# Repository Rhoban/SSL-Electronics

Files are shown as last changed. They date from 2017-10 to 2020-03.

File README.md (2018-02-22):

# SSL Boards

## Compiling firmware

Be sure you follow the README.md from https://github.com/Rhoban/Maple/ to have the prerequisite.

You can clone the `Maple` repository, for instance in your home:

    git clone git@github.com:Rhoban/Maple.git

Then, go in the firmware directory (for instance in brushless or in mainboard) and make a symlink to it:

    ln -s $HOME/Maple Maple

You can then compile and install:

    make
    make install

-------------------------------------------------

## Components

You can find most of the component source in the `FARNELL` attribute of each component.

### Main board

### Connectors

* JST-ZH 2 pin connector + cables
* JST-XH 7 pins connector for kicker board
* XT-60 connector (same as wire connector)

#### Maple mini

Board containing micro-controller (mainboard controller)

#### GY-85

9DOF IMU

#### nRF24L01 modules

2.4Ghz communication modules with short antenna (Farnell: 2143316)

### Screws

* M3 holes are on the board, on a 126x82mm rectangle.
* M3x10 spacers can be used to hold the drivers on the board

-------------------------------------------------

## Brushless driver

### Connectors

* JST-ZH 5 pin connector (for hall sensor)
* JST-ZH 6 pin connector (for encoder)
* JST-XH 3 pin connector (for motor phases)

-------------------------------------------------

## Kicker board

### Power capacitor

Power capacitors, current target is 2200uF / 200V (2102441)

### Connectors

* JST-XH 7 pins connector

#### Voltage booster

Can be easily found with keywords "390V booster"

### Screws

M3 spacers to fix the board

-------------------------------------------------

## Misc

#### Fuses

F447 fuses on the wire are used to protect

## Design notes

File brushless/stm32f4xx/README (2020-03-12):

> Copyright (C) 2019  Adrien Boussicault <adrien.boussicault@labri.fr>
>
> This program is free software: you can redistribute it and/or
> modify it under the terms of the GNU Lesser General Public
> License as published by the Free Software Foundation, either
> version 3 of the License, or (at your option) any later version.
>
> This program is distributed in the hope that it will be useful,
> but WITHOUT ANY WARRANTY; without even the implied warranty of
> MERCHANTABILITY or FITNESS FOR A PARTICULAR PURPOSE.  See the GNU
> Lesser General Public License for more details.
>
> You should have received a copy of the GNU Lesser General Public
> License along with this program.  If not, see
> <http://www.gnu.org/licenses/>.

This documentation explains how to compile the firmware of the brushless 
board, and how to flash the brushless board, by using a Linux Operating System.

##################
# Installation : #
##################

Installation commands are for Debian or Ubuntu.

Install the following package :
-------------------------------

sudo apt-get install dfu-util cu build-essential python-serial r-base

Install R libraries : 
---------------------

./tools/logs/install.r

Uninstall the modemmanager : 
----------------------------

sudo apt-get remove modemmanager

( The modemManger will grab the serial line of the USB : /dev/ttyACM0;
if you are using this service, you should prefer do desactivate them with the
following command : systemctl stop ModemManager.service )

Add Udev permition to have an access to /dev/ttyACMO
----------------------------------------------------

sudo adduser USER plugdev
sudo adduser USER dialout

Add/edit the file /etc/udev/rules.d/42-cycloide.rules and add the following 
lines :

ATTRS{idProduct}=="4567", ATTRS{idVendor}=="f123", MODE="664", GROUP="plugdev" SYMLINK+="brushless"
ATTRS{idProduct}=="5740", ATTRS{idVendor}=="0483", MODE="664", GROUP="plugdev" SYMLINK+="stm32"

The first line is dedicated to comunicate with the brushless when the firmware
is yet loaded in the board. The second one is used to flash the firmware.

Restart the udev service :
 
sudo /etc/init.d/udev restart

Normally, all should works but if you enconter some problem in the next sections, restart your computer.

Download ans install the last ARM compiler :
--------------------------------------------------

We use the gcc-arm-none-eabi compiler. You can download it at :

https://developer.arm.com/tools-and-software/open-source-software/developer-tools/gnu-toolchain/gnu-rm/downloads

Install the compiler in the root directory of the project.

You can install the compiler in another directory. In this case, 
we will explain you, in all the next sections, how to adapt the commands.

Normally, the project should looks like :
<root_directory>
├── Core
├── gcc-arm-none-eabi-XXXXXXXXX
│   ├── bin
│   ...
├── Makefile
...

Download the CMSIS source code :
--------------------------------

Install the CMSIS library in the root directory by typing :

git clone https://github.com/ARM-software/CMSIS_5.git CMSIS_5

You can install the compiler in another directory. In this case, 
we will explain you, in all the next sections, how to adapt the commands.

Normally, the project should looks like :
<root_directory>
├── Core
├── CMSIS_5
│   ├── CMSIS
│   ...
├── Makefile
...

OPTIONAL INSTALLATION (to use JTAG):
-------------------------------------

You can install JLink tools in order to use JTAG to flash or print.
Go to the website :  

https://www.segger.com/downloads/jlink/

And install the J-Link Software and Documentation Pack :
    - download the debian package (file finishing with .deb)
    - install it : sudo dpkg --install XXX.deb
      where XXX.deb is the name downloaded file.

OPTIONAL INSTALLAION OF CUBEMX (to update the source code autgenerated by cubeMX ):
-----------------------------------------------------------------------------------

If you want to change the configuration generated by CUBEMX, you have to install
CubeMX for the following website :

https://www.st.com/en/development-tools/stm32cubemx.html

#########################################
# Compile the application               #
#########################################

Just type

make

If you have installed GCC and CMSIS in an unusual place, then you have to type :

make GCC_PATH=<ARM_DIRECTORY>/bin CMSIS_PATH=<CMSIS_5_PATH>/CMSIS

otherwise, you just have to add two symbolic links in your root directory :

cd <root directory>
ln -s ARM_DIRECTIRY gcc-arm-none-eabi
ln -s CMSIS_5_DIRECTIRY CMSIS_5

###################
# Flash the board #
###################

Three solutions are possible depending of the situation.
IF THE BOARD HAVE NOT YET BEEN FLASHED, YOU SHOULD USE (as you want) SOLUTION 
1) OR 2).
Solution 3) is the most simple one and it is used to update the firmware (we 
need the board to be yet flashed).

Short description of the 3 solutions : 
 1) FLASH BY USB USING THE RESET AND BOOT0 BUTTONS
   This solution doesn't need the board to be yet flashed.
   This solution need USB wire and and an access to the BOOT0 and RESET buttons
   of the board.
 2) FLASH BY JTAG USING THE JLink SOFWTARE
   This solution doesn't need the board to be yet flashed.
   This solution need an USB wire (for the power) and a JTAG for the connection.
   This solution Use JLink software (see Optional installation)
   The JLink software downloads just the part of the memory that have changed.
   So the flash operation are fast and the life of the flash memory is 
   increased.
 3) FLASH BY USB WITHOUT USING THE RESET BUTTONS
   This solution need the board to be yet flashed
   ( by using 1) or 2) for example ).
   This solution just need a USB wire ! :)
   This solution DO NOT require an acess to the BOOT0 and RESET button ! :)

1) FLASH BY USB USING THE RESET AND BOOT0 BUTTONS

 Connect the USB wire.

 Press and hold the BOOT0 button, then press and realease de RESET button,
 and finally release the BOOT0 button.

 Type the command :
 ./first_flash_with_usb_and_reset_button.sh

2) FLASH BY JTAG USING THE JLink SOFWTARE

 ./jtag_flash.sh

3) FLASH BY USB WITHOUT THE RESET BUTTONS

 ./usb_flash.sh

########################
# Connect to the board #
########################

First Connect the USB wire.

To know on which device the board is connected (usualy it is /dev/ttyACM0),
you have to execute the following command :

dmesg

The output should looks like : 

   [112520.828609] usb 1-5: new full-speed USB device number 59 using xhci_hcd
   [112520.979771] usb 1-5: New USB device found, idVendor=f123, idProduct=4567, bcdDevice= 2.00
   [112520.979777] usb 1-5: New USB device strings: Mfr=1, Product=2, SerialNumber=3
   [112520.979780] usb 1-5: Product: Brushless Driver
   [112520.979783] usb 1-5: Manufacturer: OpenHandicap
   [112520.979785] usb 1-5: SerialNumber: 346F398B3038
   [112520.981964] cdc_acm 1-5:1.0: ttyACM0: USB ACM device

and the serial port is ttyACM0, so the device is connected on (/def/ttyACM0).

Open a command line into the board by typing:

cu -l /dev/ttyACM0

Your are connected to the boare. Enjoy :) 
(In the command line, help is the first helpfull command to know)
(type 'led' to turn on/off the led of the board) 

OPTIONAL :
----------
Some informations are sent using the jtag link. (just some small messages 
to prevent warnings and errors). Those messages appear in the terminal too.

If you want to read the jtag output, you need to install JLink (see the
optional section on JTag), and then, you just have to type : 

./print_jtag

Jtag is usefull for developpers.

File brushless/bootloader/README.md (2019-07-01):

# Maple Bootloader for Robotis boards

This is an adaptation of the maple bootloader in order to make it work with the
Robotis CM900 and OpenCM9.04 boards:

* [Robotis CM900](http://support.robotis.com/en/product/auxdevice/controller/cm-900_manual.htm)
* [Robotis OpenCM9.04](http://support.robotis.com/en/product/auxdevice/controller/opencm9.04.htm)

## How to install it?

### The easy way

#### OpenCM9.04

The easy way is to use a simple sketch with the robotis OpenCM Framework to do it. Simply run
OpenCM IDE and open the `opencm904_maple_loader` sketch that is in the `sketch/` directory of
this repository.

**If you load that sketch, it will rewrite your bootloader to the OpenCM9.04 bootloader;
OpenCM IDE won't work anymore!**

Wait until your board led blinks, and your bootloader should be changed. You can press the reset
button and you should see the "bootloader blink".

### The standard way

#### Step 1. Build or get the right bootloader

You can either build it or get it (from the `snapshot` directory). See below.

#### Step 2. Wire a serial line to your board

This step may require some soldering or electronic hacking, you'll have to wire up a serial 3.3V 
adapter. You can for instance use a [3.3V FTDI cable](http://www.ftdichip.com/Products/Cables/USBTTLSerial.htm)
or a [3.3V FTDI Breakout](https://www.sparkfun.com/products/retired/8772). 5V logic should also
work with this.

Then, wire your serial adapter to the Serial1 (TX1 and RX1) pins of your board.

#### Step 3. Put your board in hardware bootloader mode

Press the RESET button of your board, and then put the BOOT0 signal to 3.3V (this can be done
with an extra wire), release the RESET button, and release the BOOT0.

#### Step 4. Flash the bootloader!

You can now flash the bootloader:

```
# You may have to adapt the serial port, this is an example:
python stm32loader.py -p /dev/ttyUSB -evw bootloader.bin
```

Tada! It should then be OK.

### What's next?

Next, you can program your board using `dfu-util`. This is done by default in the libmaple
Makefile.

You can now use `cm900` and `opencm904` variants in the LibMaple, or use the RobotsWar 
framework
https://github.com/RobotsWar/RobotsWar

## Boards

### CM900

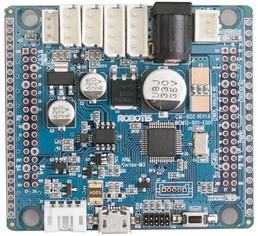
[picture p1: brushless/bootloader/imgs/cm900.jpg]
CM900


The `master` branch of this repository is supporting CM900 board, you can find a
snapshot of the bootloader in `snapshot/maple-boot-cm900.bin`.

### OpenCM9.04

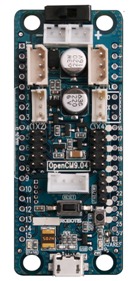
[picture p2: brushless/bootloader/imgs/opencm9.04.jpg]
OpenCM9.04


Ths `opencm904` branch of this repository is supporting the OpenCM9.04 board. You can
find a snapshot of this bootloader in `snapshot/maple-boot-opencm904.bin`.

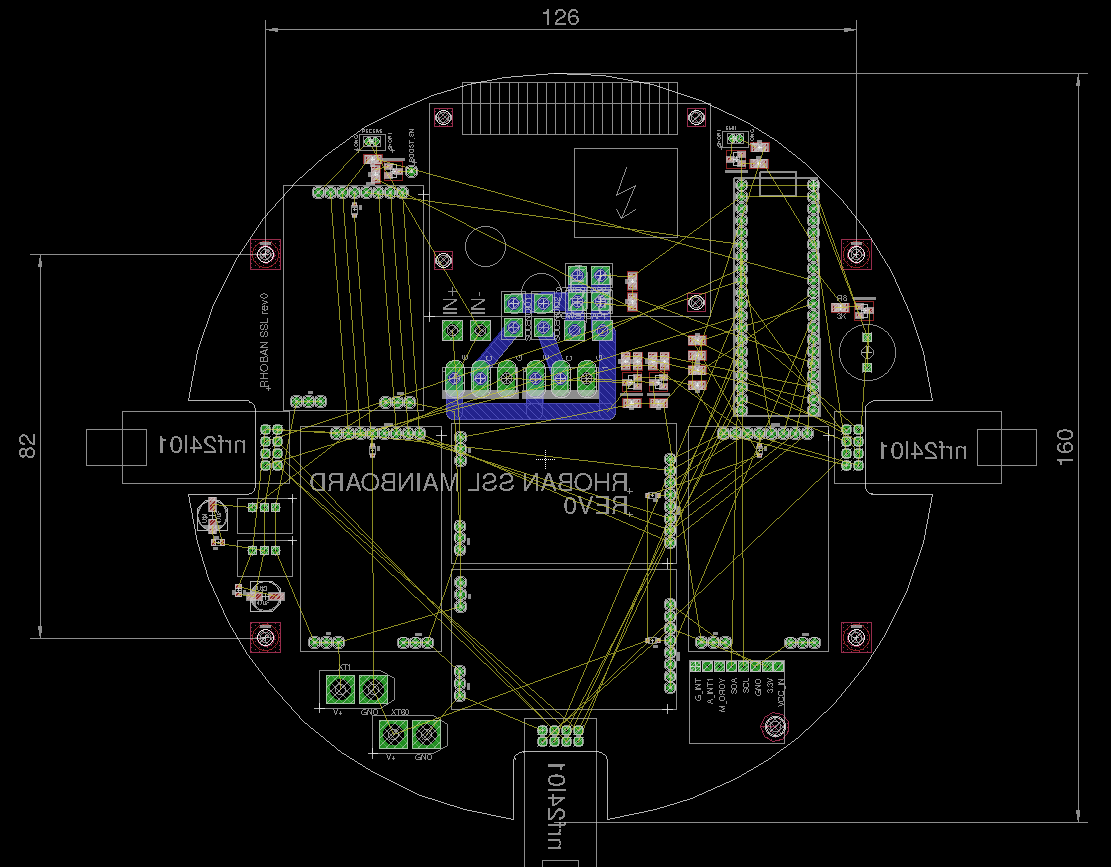
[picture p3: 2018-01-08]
mainboard/dimensions.png

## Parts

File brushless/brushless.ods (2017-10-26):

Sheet: brushless
Farnell | Name | Value | Device | Package
1437637 | BUT | KMR211GLFS | BUTTON-KMR241GLFS | PUSHBUTTON-KMR241GLFS
2528772 | C1 | 10µF | 0.33UF/330NF-0805-50V-10% | 805
2528772 | C2 | 10µF | 0.33UF/330NF-0805-50V-10% | 805
2528772 | C3 | 10µF | 0.33UF/330NF-0805-50V-10% | 805
2496935 | C4 | 1000pF | CAP0805 | 0805@1
2496946 | C7 | 1uF | CAP0805 | 0805@1
1144713 | C10 | 100uF | CPOL_EU_3.5-8 | E3,5-8
2496946 | C12 | 1uF | CAP0805 | 0805@1
721980 | C17 | 15pF | C_EU_22PF | C0603
721980 | C18 | 15pF | C_EU_22PF | C0603
1414620 | C20 | 18pF | CAP0805 | 0805@1
1414620 | C21 | 18pF | CAP0805 | 0805@1
2317446 | D1 |  | ZETEX_VAR2SOT23 | ZETEX_SOT-23
2317446 | D2 |  | ZETEX_VAR2SOT23 | ZETEX_SOT-23
2317446 | D3 |  | ZETEX_VAR2SOT23 | ZETEX_SOT-23
1581233 | D4 | Blue | LED1206 | LED-1206
8737843RL | D5 |  | DIODESOD | SOD-323
2296000 | DRV1 | OPEN-BLDC_IR2101 | OPEN-BLDC_IR2101 | OPEN-BLDC_SO-8
2296000 | DRV2 | OPEN-BLDC_IR2101 | OPEN-BLDC_IR2101 | OPEN-BLDC_SO-8
2296000 | DRV3 | OPEN-BLDC_IR2101 | OPEN-BLDC_IR2101 | OPEN-BLDC_SO-8
- | ENC1 | LS7366RSO14 | LS7366RSO14 | SO14
1022248 | GND | CONNEC_1X03 | CONNEC_1X03 | CONNEC_1X03
- | JP1 | JUMPER-SMT_2_NO_NO-SILK_ROUND | JUMPER-SMT_2_NO_NO-SILK_ROUND | SMT-JUMPER_2_NO_NO-SILK_ROUND
- | JP2 | JUMPER-SMT_2_NO_NO-SILK_ROUND | JUMPER-SMT_2_NO_NO-SILK_ROUND | SMT-JUMPER_2_NO_NO-SILK_ROUND
2470830 | K1 |  | 614105150721 | 614105150721
1022256 | LOGIC | CONNEC_1X08 | CONNEC_1X08 | CONNEC_1X08
2467818 | OSC | 8MHz | CRYSTAL5X3 | CRYSTAL-SMD-5X3
1842013 | OSC1 | 40Mhz | CRYSTAL5X3 | CRYSTAL-SMD-5X3
2319916 | Q1 | BUK7Y12-40E | BUK7Y12-40E | SOT669
2319916 | Q2 | BUK7Y12-40E | BUK7Y12-40E | SOT669
2319916 | Q3 | BUK7Y12-40E | BUK7Y12-40E | SOT669
2319916 | Q4 | BUK7Y12-40E | BUK7Y12-40E | SOT669
2319916 | Q5 | BUK7Y12-40E | BUK7Y12-40E | SOT669
2319916 | Q6 | BUK7Y12-40E | BUK7Y12-40E | SOT669
2446904 | R1 | 1K | RESISTOR0805 | 805
2446904 | R2 | 1K | RESISTOR0805 | 805
2446904 | R3 | 1K | RESISTOR0805 | 805
2446904 | R4 | 1K | RESISTOR0805 | 805
2446904 | R5 | 1K | RESISTOR0805 | 805
2446904 | R6 | 1K | RESISTOR0805 | 805
2447553 | R7 | 10K | RESISTOR0805 | 805
2447553 | R8 | 10K | RESISTOR0805 | 805
2447553 | R9 | 10K | RESISTOR0805 | 805
2447553 | R10 | 10K | RESISTOR0805 | 805
2447553 | R11 | 10K | RESISTOR0805 | 805
2447553 | R12 | 10K | RESISTOR0805 | 805
2447553 | R14 | 10K | RESISTOR0805 | 805
2447553 | R15 | 10K | RESISTOR0805 | 805
2447553 | R16 | 10K | RESISTOR0805 | 805
2447553 | R17 | 10K | RESISTOR0805 | 805
2447553 | R18 | 10K | RESISTOR0805 | 805
2447553 | R19 | 10K | RESISTOR0805 | 805
2446939 | R20 | 2K | RESISTOR0805 | 805
2446965 | R21 | 3K | RESISTOR0805 | 805
2447553 | R23 | 10K | RESISTOR0805 | 805
2447553 | R24 | 10K | RESISTOR0805 | 805
2447553 | R25 | 10K | RESISTOR0805 | 805
2446909 | R28 | 1.5K | RESISTOR0805 | 805
2446926 | R29 | 22 | RESISTOR0805 | 805
2446926 | R35 | 22 | RESISTOR0805 | 805
2446904 | R36 | 1K | RESISTOR0805 | 805
2446904 | R39 | 1K | RESISTOR0805 | 805
2447553 | R40 | 10K | RESISTOR0805 | 805
2447553 | R48 | 10K | RESISTOR0805 | 805
2446904 | R49 | 1K | RESISTOR0805 | 805
2447553 | R50 | 10K | RESISTOR0805 | 805
7261403 | REG1 | TS2940CW-3.3RP | TS2940CW-3.3RP | SOT223
1437637 | RESET | KMR211GLFS | BUTTON-KMR241GLFS | PUSHBUTTON-KMR241GLFS
1329624 | SENSE | ACS712 | ACS712 | SO8
1606327 | UC1 | STM32F103CBT6 | STM32F103CB | LQFP48
1022248 | V+ | CONNEC_1X03 | CONNEC_1X03 | CONNEC_1X03
- | X1 | JST-XH-10-PIN-LONG-PAD | JST-XH-10-PIN-LONG-PAD | JST-XH-10-PACKAGE-LONG-PAD

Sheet: Pivot Table_brushless_1
Farnell | Name | Value | Device | Package | (empty)
721980 | C17 | 15pF | C_EU_22PF | C0603
 | C18 | 15pF | C_EU_22PF | C0603
1022248 | GND | CONNEC_1X03 | CONNEC_1X03 | CONNEC_1X03
 | V+ | CONNEC_1X03 | CONNEC_1X03 | CONNEC_1X03
1022256 | LOGIC | CONNEC_1X08 | CONNEC_1X08 | CONNEC_1X08
1144713 | C10 | 100uF | CPOL_EU_3.5-8 | E3,5-8
1329624 | SENSE | ACS712 | ACS712 | SO8
1414620 | C20 | 18pF | CAP0805 | 0805@1
 | C21 | 18pF | CAP0805 | 0805@1
1437637 | BUT | KMR211GLFS | BUTTON-KMR241GLFS | PUSHBUTTON-KMR241GLFS
 | RESET | KMR211GLFS | BUTTON-KMR241GLFS | PUSHBUTTON-KMR241GLFS
1581233 | D4 | Blue | LED1206 | LED-1206
1606327 | UC1 | STM32F103CBT6 | STM32F103CB | LQFP48
1842013 | OSC1 | 40Mhz | CRYSTAL5X3 | CRYSTAL-SMD-5X3
2296000 | DRV1 | OPEN-BLDC_IR2101 | OPEN-BLDC_IR2101 | OPEN-BLDC_SO-8
 | DRV2 | OPEN-BLDC_IR2101 | OPEN-BLDC_IR2101 | OPEN-BLDC_SO-8
 | DRV3 | OPEN-BLDC_IR2101 | OPEN-BLDC_IR2101 | OPEN-BLDC_SO-8
2317446 | D1 | (empty) | ZETEX_VAR2SOT23 | ZETEX_SOT-23
 | D2 | (empty) | ZETEX_VAR2SOT23 | ZETEX_SOT-23
 | D3 | (empty) | ZETEX_VAR2SOT23 | ZETEX_SOT-23
2319916 | Q1 | BUK7Y12-40E | BUK7Y12-40E | SOT669
 | Q2 | BUK7Y12-40E | BUK7Y12-40E | SOT669
 | Q3 | BUK7Y12-40E | BUK7Y12-40E | SOT669
 | Q4 | BUK7Y12-40E | BUK7Y12-40E | SOT669
 | Q5 | BUK7Y12-40E | BUK7Y12-40E | SOT669
 | Q6 | BUK7Y12-40E | BUK7Y12-40E | SOT669
2446904 | R1 | 1K | RESISTOR0805 | 805
 | R2 | 1K | RESISTOR0805 | 805
 | R3 | 1K | RESISTOR0805 | 805
 | R36 | 1K | RESISTOR0805 | 805
 | R39 | 1K | RESISTOR0805 | 805
 | R4 | 1K | RESISTOR0805 | 805
 | R49 | 1K | RESISTOR0805 | 805
 | R5 | 1K | RESISTOR0805 | 805
 | R6 | 1K | RESISTOR0805 | 805
2446909 | R28 | 1.5K | RESISTOR0805 | 805
2446926 | R29 | 22 | RESISTOR0805 | 805
 | R35 | 22 | RESISTOR0805 | 805
2446939 | R20 | 2K | RESISTOR0805 | 805
2446965 | R21 | 3K | RESISTOR0805 | 805
2447553 | R10 | 10K | RESISTOR0805 | 805
 | R11 | 10K | RESISTOR0805 | 805
 | R12 | 10K | RESISTOR0805 | 805
 | R14 | 10K | RESISTOR0805 | 805
 | R15 | 10K | RESISTOR0805 | 805
 | R16 | 10K | RESISTOR0805 | 805
 | R17 | 10K | RESISTOR0805 | 805
 | R18 | 10K | RESISTOR0805 | 805
 | R19 | 10K | RESISTOR0805 | 805
 | R23 | 10K | RESISTOR0805 | 805
 | R24 | 10K | RESISTOR0805 | 805
 | R25 | 10K | RESISTOR0805 | 805
 | R40 | 10K | RESISTOR0805 | 805
 | R48 | 10K | RESISTOR0805 | 805
 | R50 | 10K | RESISTOR0805 | 805
 | R7 | 10K | RESISTOR0805 | 805
 | R8 | 10K | RESISTOR0805 | 805
 | R9 | 10K | RESISTOR0805 | 805
2467818 | OSC | 8MHz | CRYSTAL5X3 | CRYSTAL-SMD-5X3
2470830 | K1 | (empty) | 614105150721 | 614105150721
2496935 | C4 | 1000pF | CAP0805 | 0805@1
2496946 | C12 | 1uF | CAP0805 | 0805@1
 | C7 | 1uF | CAP0805 | 0805@1
2528772 | C1 | 10µF | 0.33UF/330NF-0805-50V-10% | 805
 | C2 | 10µF | 0.33UF/330NF-0805-50V-10% | 805
 | C3 | 10µF | 0.33UF/330NF-0805-50V-10% | 805
7261403 | REG1 | TS2940CW-3.3RP | TS2940CW-3.3RP | SOT223
- | ENC1 | LS7366RSO14 | LS7366RSO14 | SO14
 | JP1 | JUMPER-SMT_2_NO_NO-SILK_ROUND | JUMPER-SMT_2_NO_NO-SILK_ROUND | SMT-JUMPER_2_NO_NO-SILK_ROUND
 | JP2 | JUMPER-SMT_2_NO_NO-SILK_ROUND | JUMPER-SMT_2_NO_NO-SILK_ROUND | SMT-JUMPER_2_NO_NO-SILK_ROUND
 | X1 | JST-XH-10-PIN-LONG-PAD | JST-XH-10-PIN-LONG-PAD | JST-XH-10-PACKAGE-LONG-PAD
8737843RL | D5 | (empty) | DIODESOD | SOD-323
Total Result

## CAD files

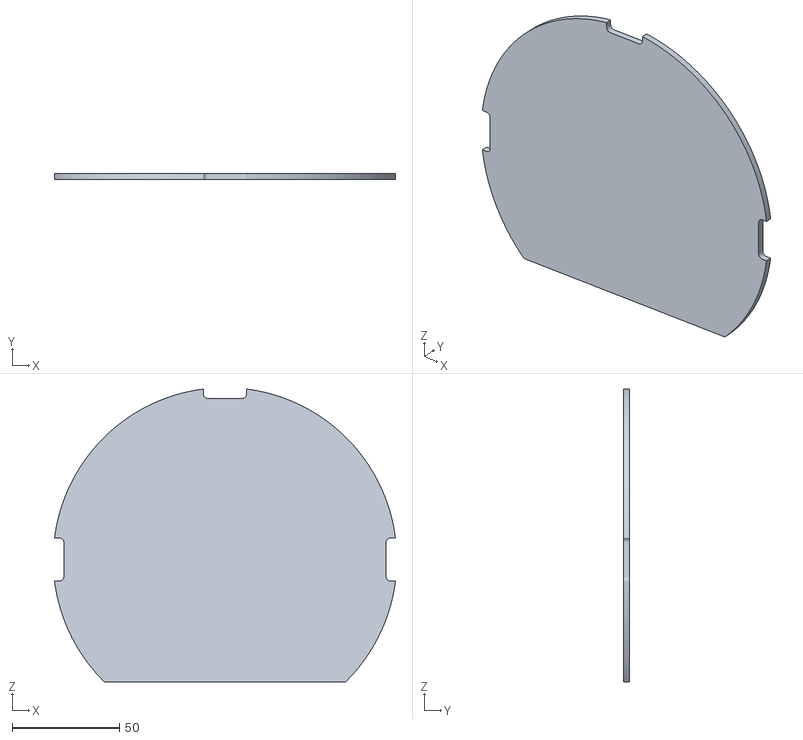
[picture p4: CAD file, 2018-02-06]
mainboard/shape/board.stl
158.7 x 3.00 x 136.4

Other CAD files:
mainboard/shape/board.dxf
mainboard/shape/board.ipt

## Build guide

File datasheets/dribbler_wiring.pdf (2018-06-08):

# Dribbler wiring

## Dribbler Connection

Brown
Red
Orange

Yellow
Green
Blue
Violet
Grey

JST-XH black (ext)
JST-XH black (mid.)
JST-XH red

Hall black
Hall red
Hall yellow
Hall green
Hall blue

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
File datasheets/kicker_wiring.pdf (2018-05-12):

Kicker board
connector view

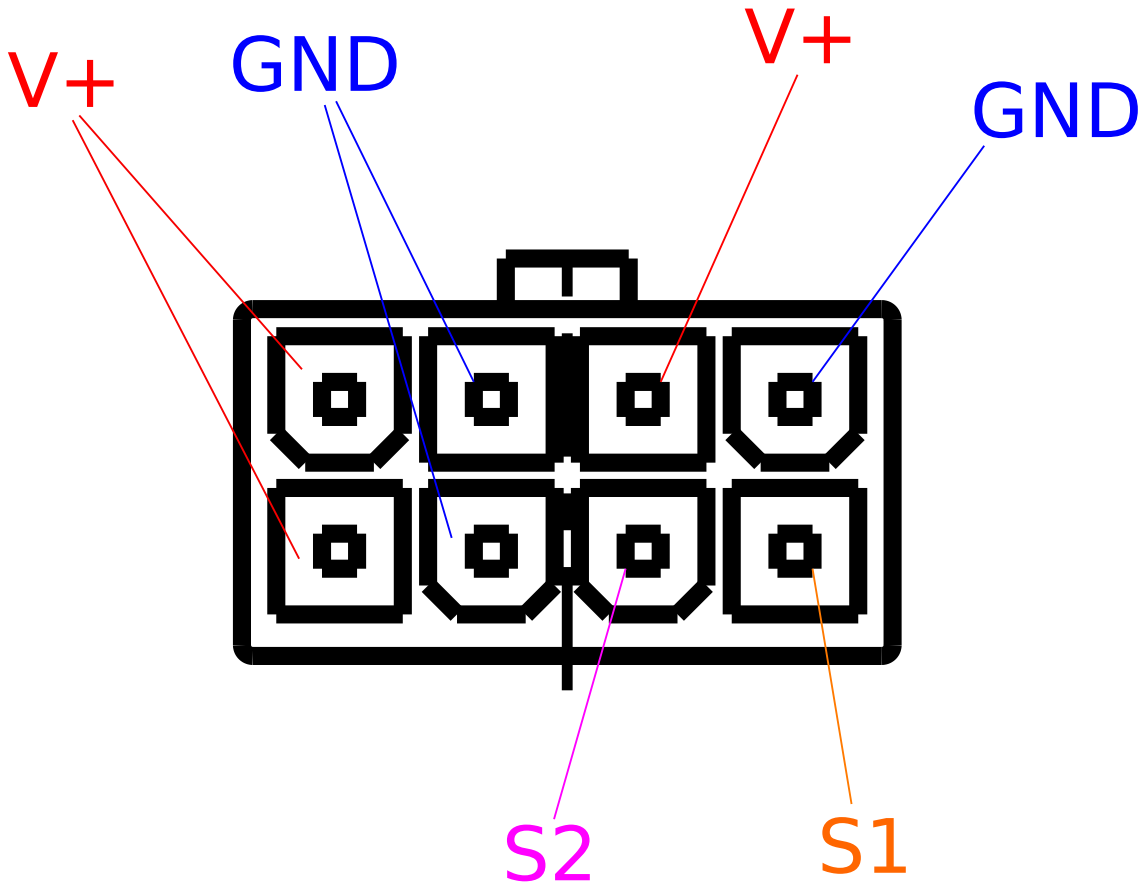
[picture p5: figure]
GND

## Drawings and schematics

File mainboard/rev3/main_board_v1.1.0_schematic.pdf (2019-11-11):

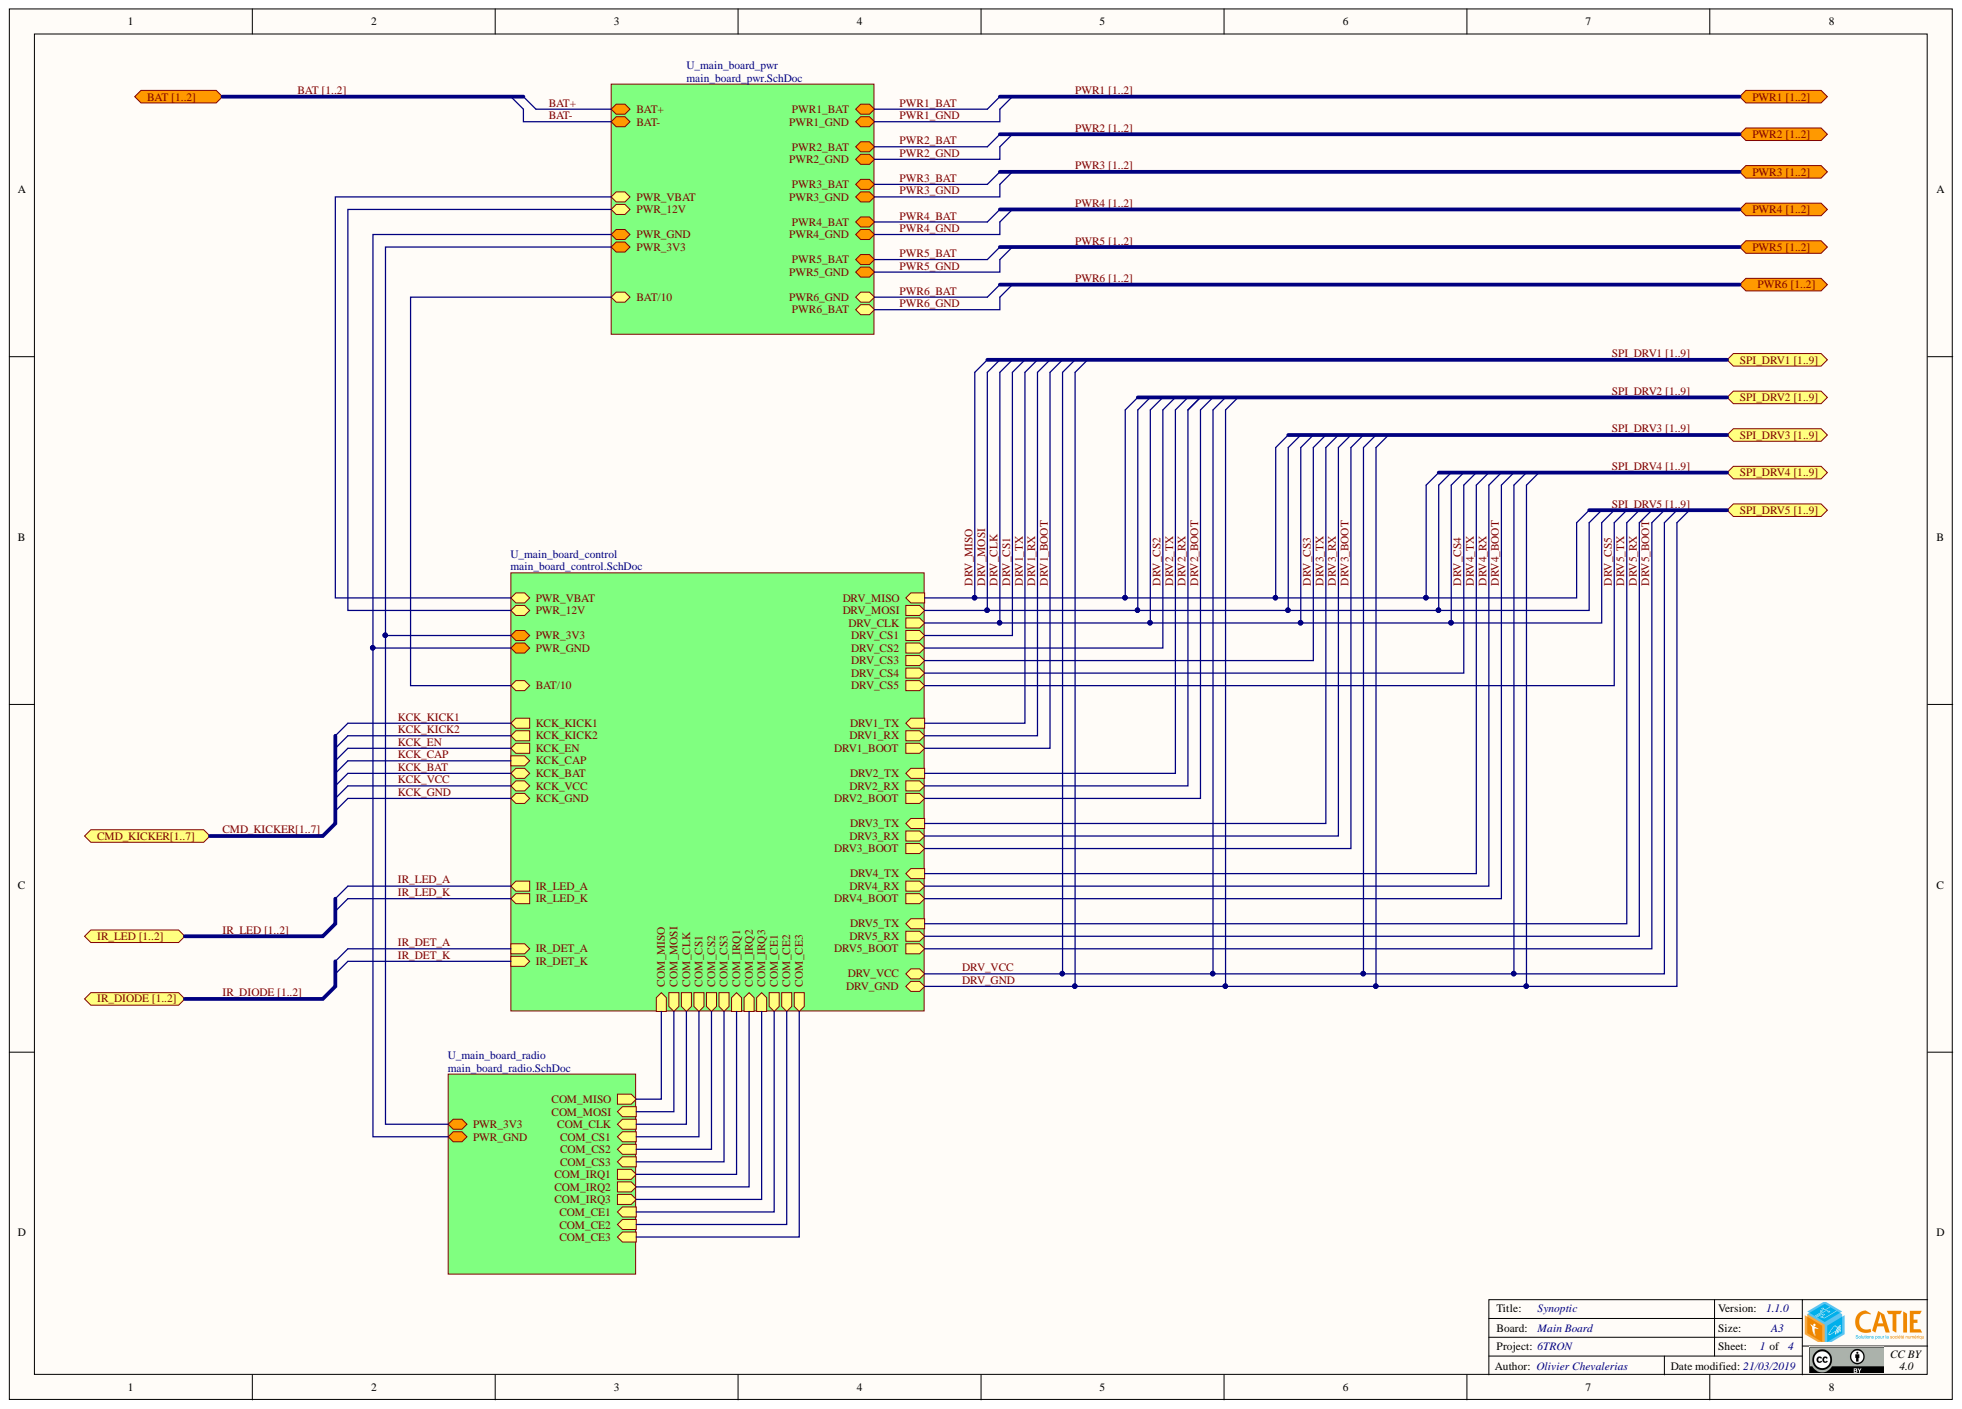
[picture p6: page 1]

PWR_VBAT PWR_12V

PWR_3V3

KCK_KICK2
KCK_EN
KCK_CAP
KCK_BAT
KCK_VCC
KCK_GND

IR_LED_A
IR_LED_K

IR_DET_A
IR_DET_K | DRV_VCC

Title: Synoptic | Version: 1.1.0
Board: Main Board | Size: A3
Project: 6TRON | Sheet: 1 of 4
Author: Olivier Chevalerias | Date modified: 21/03/2019

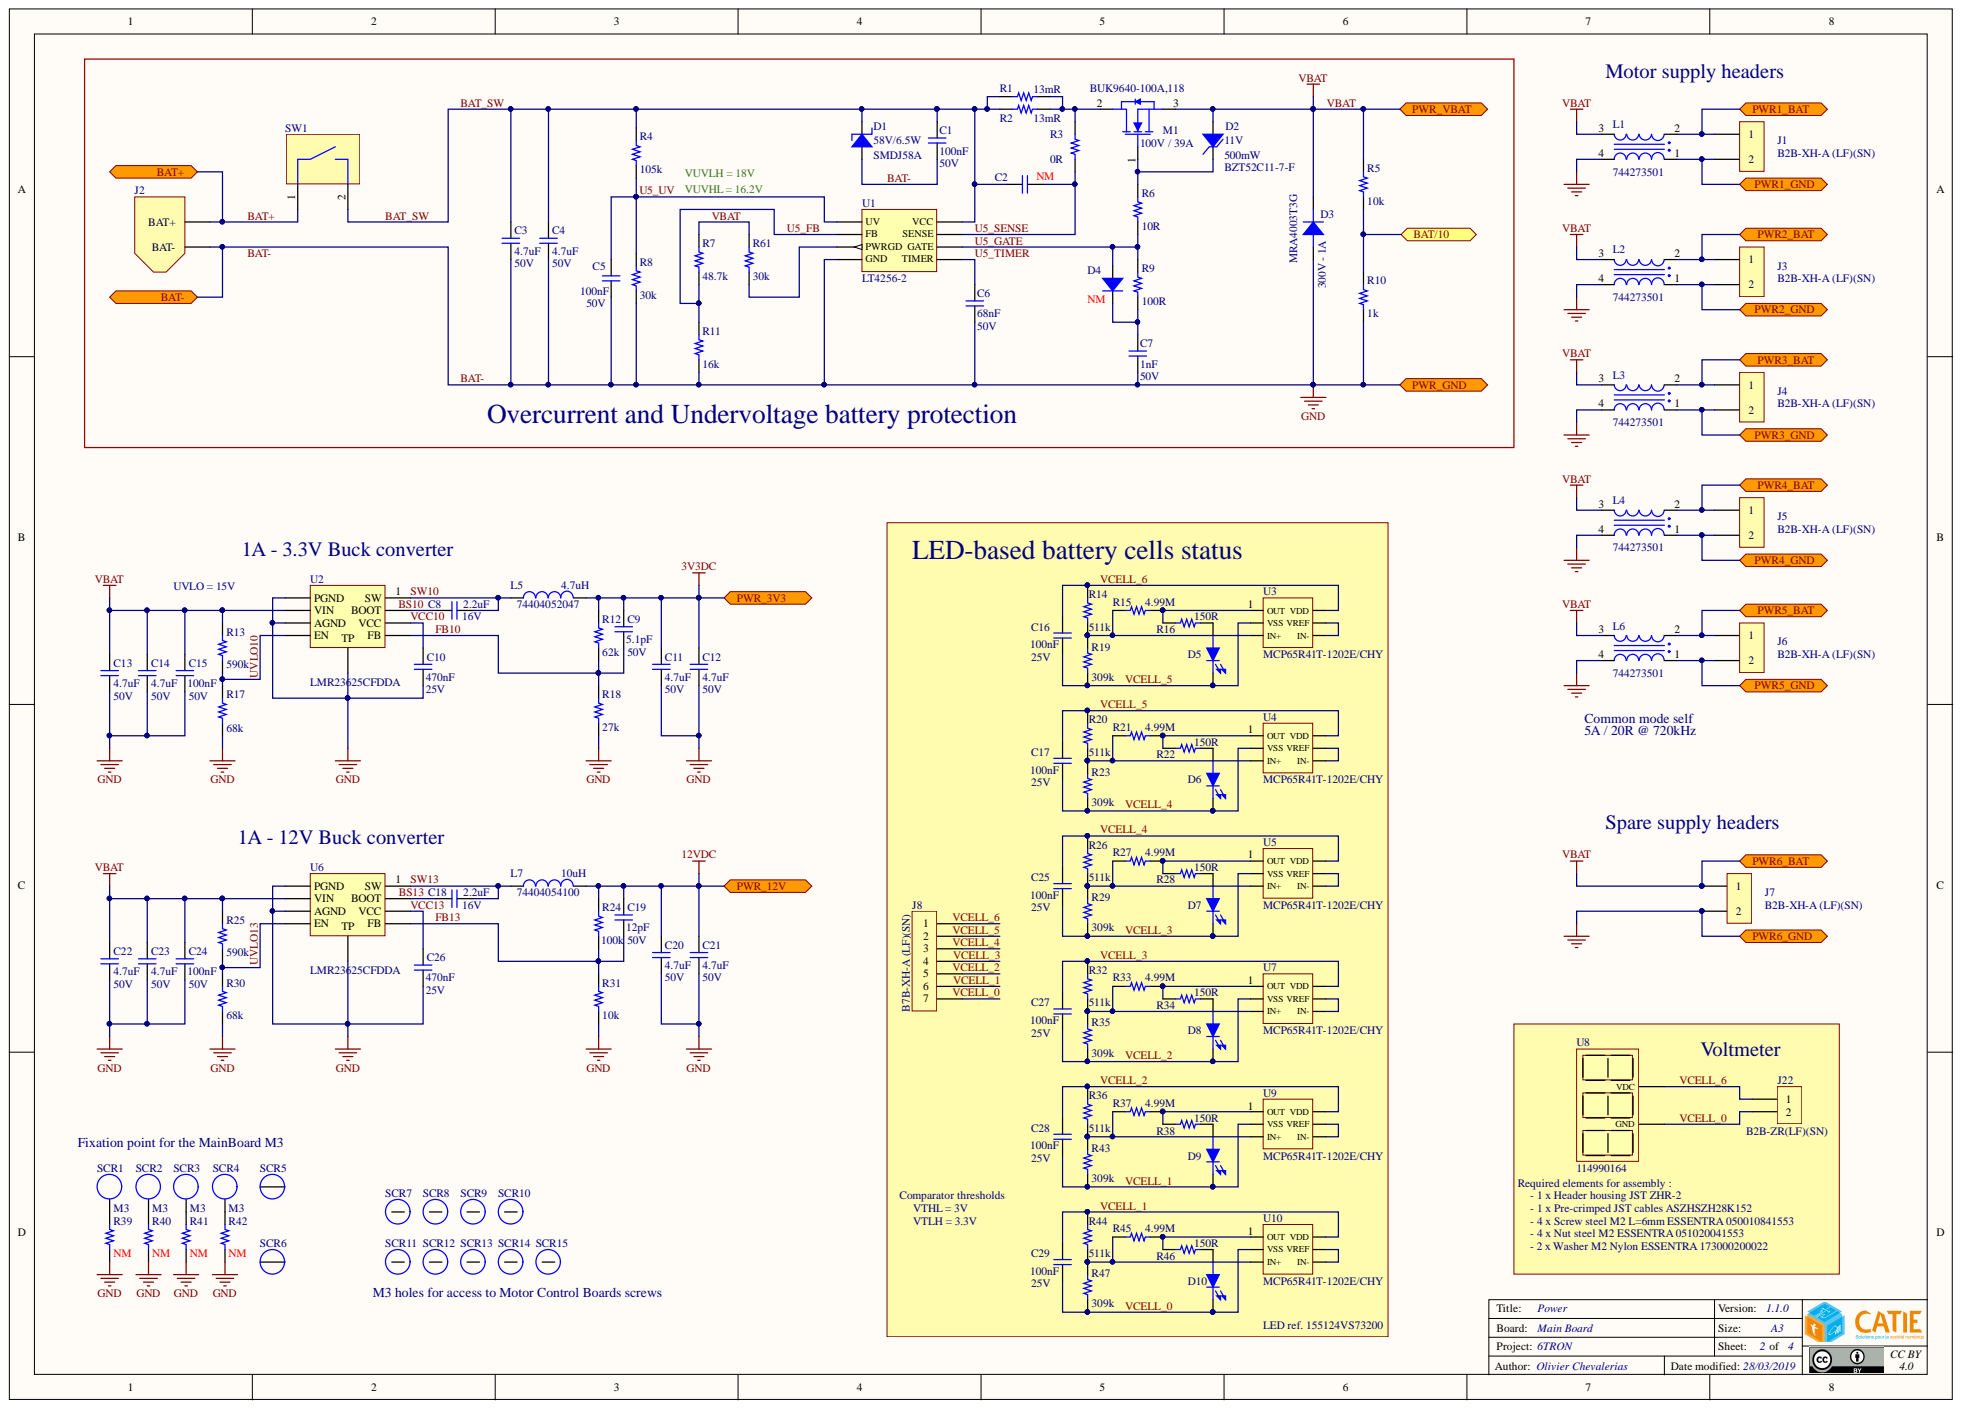
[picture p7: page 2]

BAT-
Overcurrent and Undervoltage battery protection

LED-based battery cells status

Fixation point for the MainBoard M3

Required elements for assembly :
- 1 x Header housing JST ZHR-2
- 1 x Pre-crimped JST cables ASZHSZH28K152

M3 holes for access to Motor Control Boards screws

Project: 6TRON | 2 4

Olivier Chevalerias | 28/03/2019

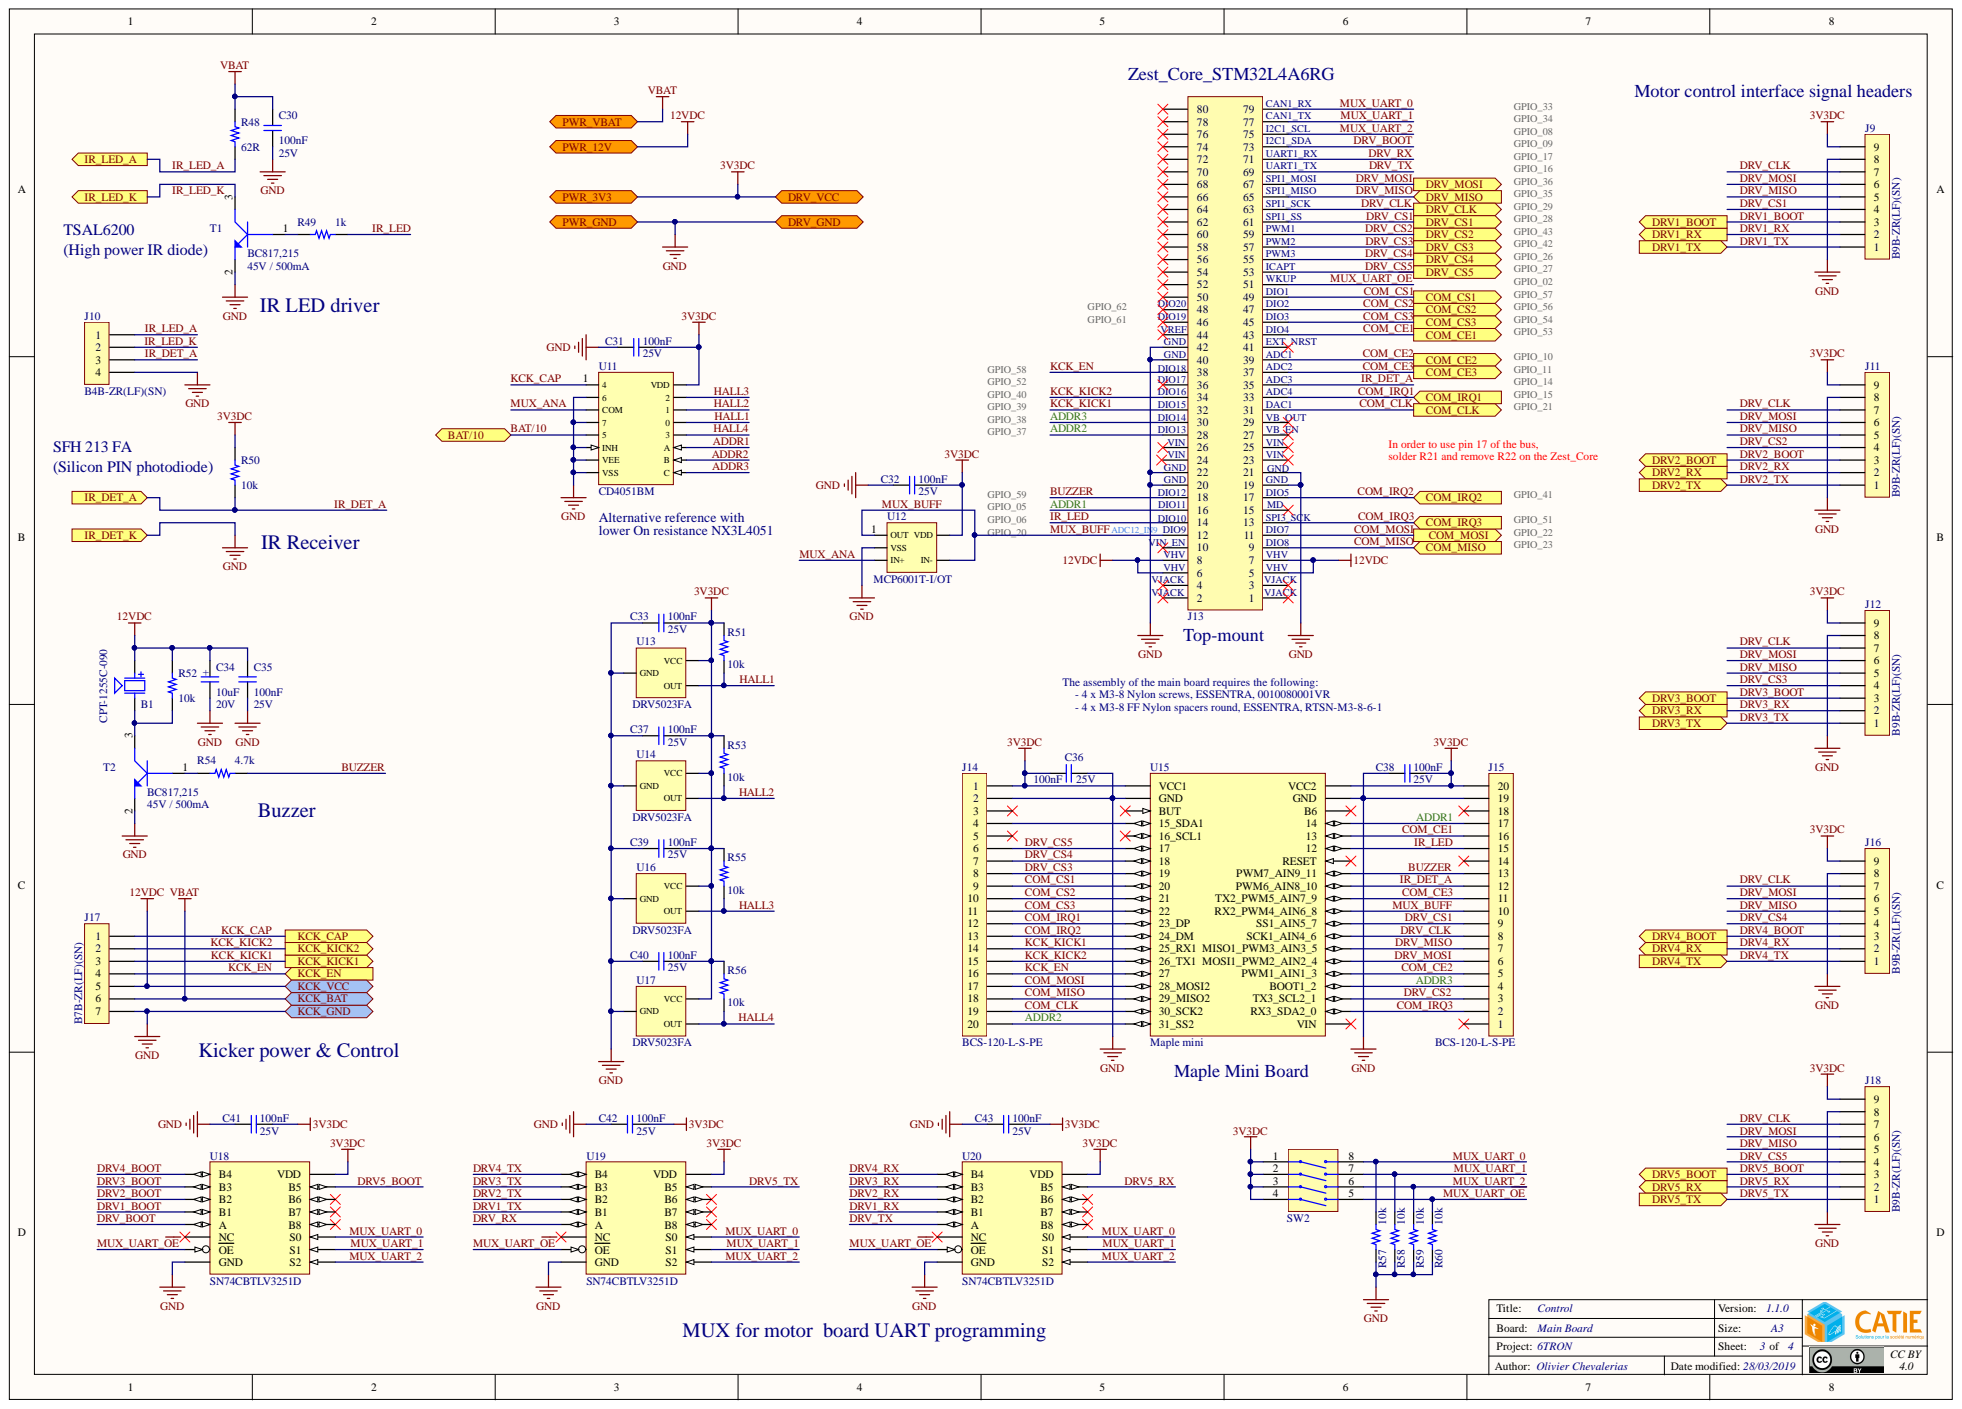
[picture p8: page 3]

Motor control interface signal headers

TSAL6200
(High power IR diode)

In order to use pin 17 of the bus,
solder R21 and remove R22 on the Zest_Core

VIN | | VIN
GND | | GND
DIO12 DIO10 | DIO11 DIO9 | | DIO5

Alternative reference with lower On resistance NX3L4051

VIN_EN | | DIO8
VHV | | VHV
VJACK | | | VJACK

The assembly of the main board requires the following:
- 4 x M3-8 Nylon screws, ESSENTRA, 0010080001VR
- 4 x M3-8 FF Nylon spacers round, ESSENTRA, RTSN-M3-8-6-1

ADDR1

DRV_CS5 | | COM_CE1

IR_LED

COM_CS2 | COM_CE3
COM_CS3 | MUX_BUFF
COM_IRQ1 | DRV_CS1

KCK_KICK1 | DRV_MISO
KCK_KICK2 | DRV_MOSI

COM_CLK | COM_IRQ3
ADDR2

MUX for motor board UART programming

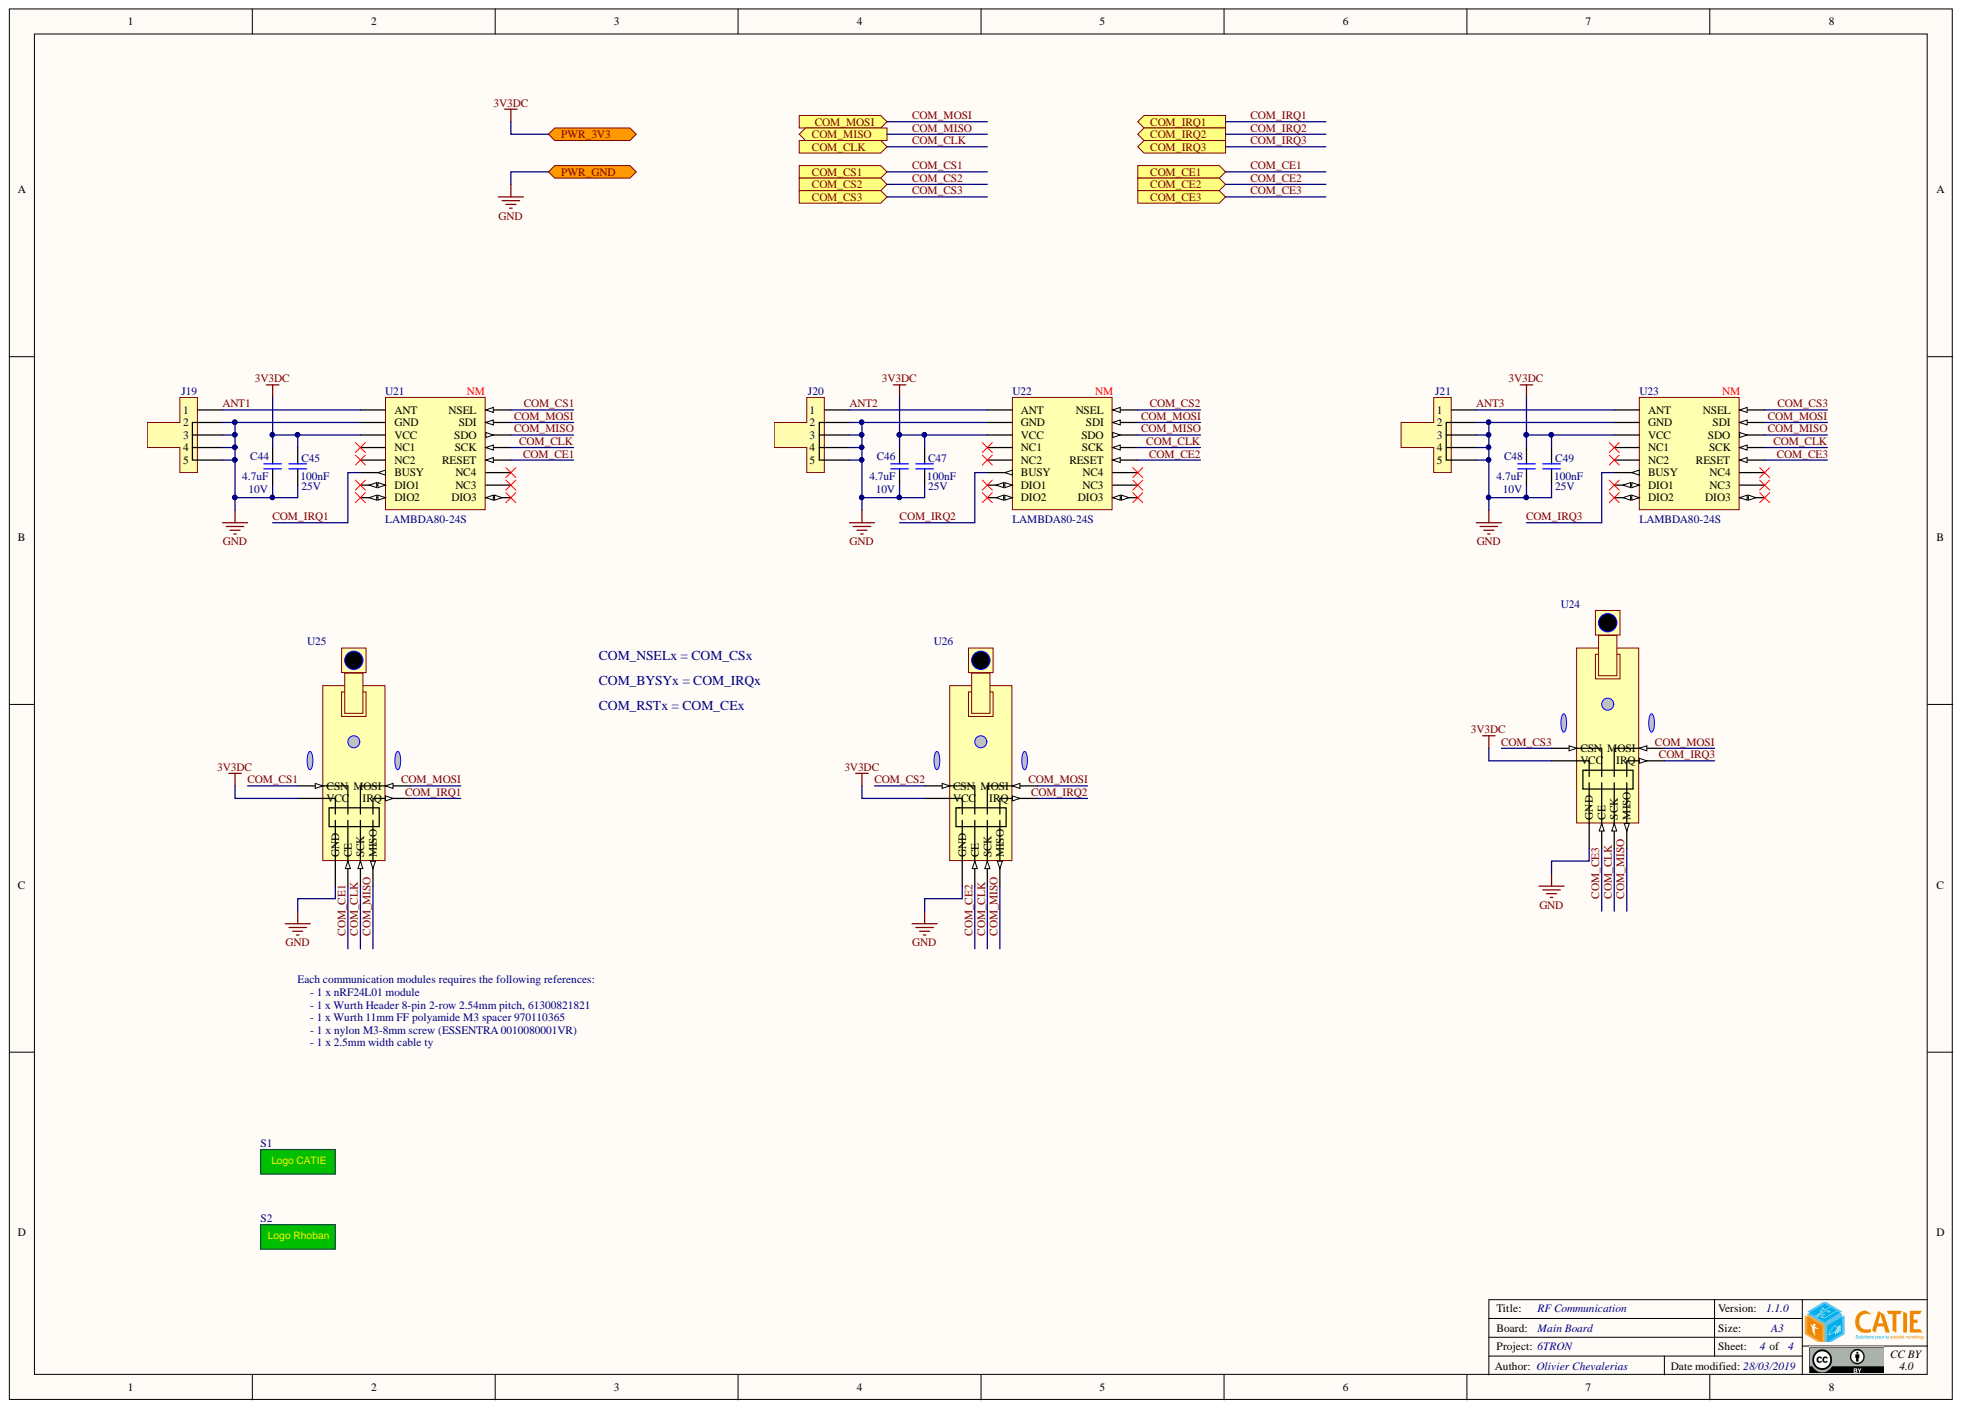
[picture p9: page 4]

Each communication modules requires the following references:
- 1 x nRF24L01 module
- 1 x Wurth Header 8-pin 2-row 2.54mm pitch, 61300821821
- 1 x Wurth 11mm FF polyamide M3 spacer 970110365
- 1 x nylon M3-8mm screw (ESSENTRA 0010080001VR)
- 1 x 2.5mm width cable ty

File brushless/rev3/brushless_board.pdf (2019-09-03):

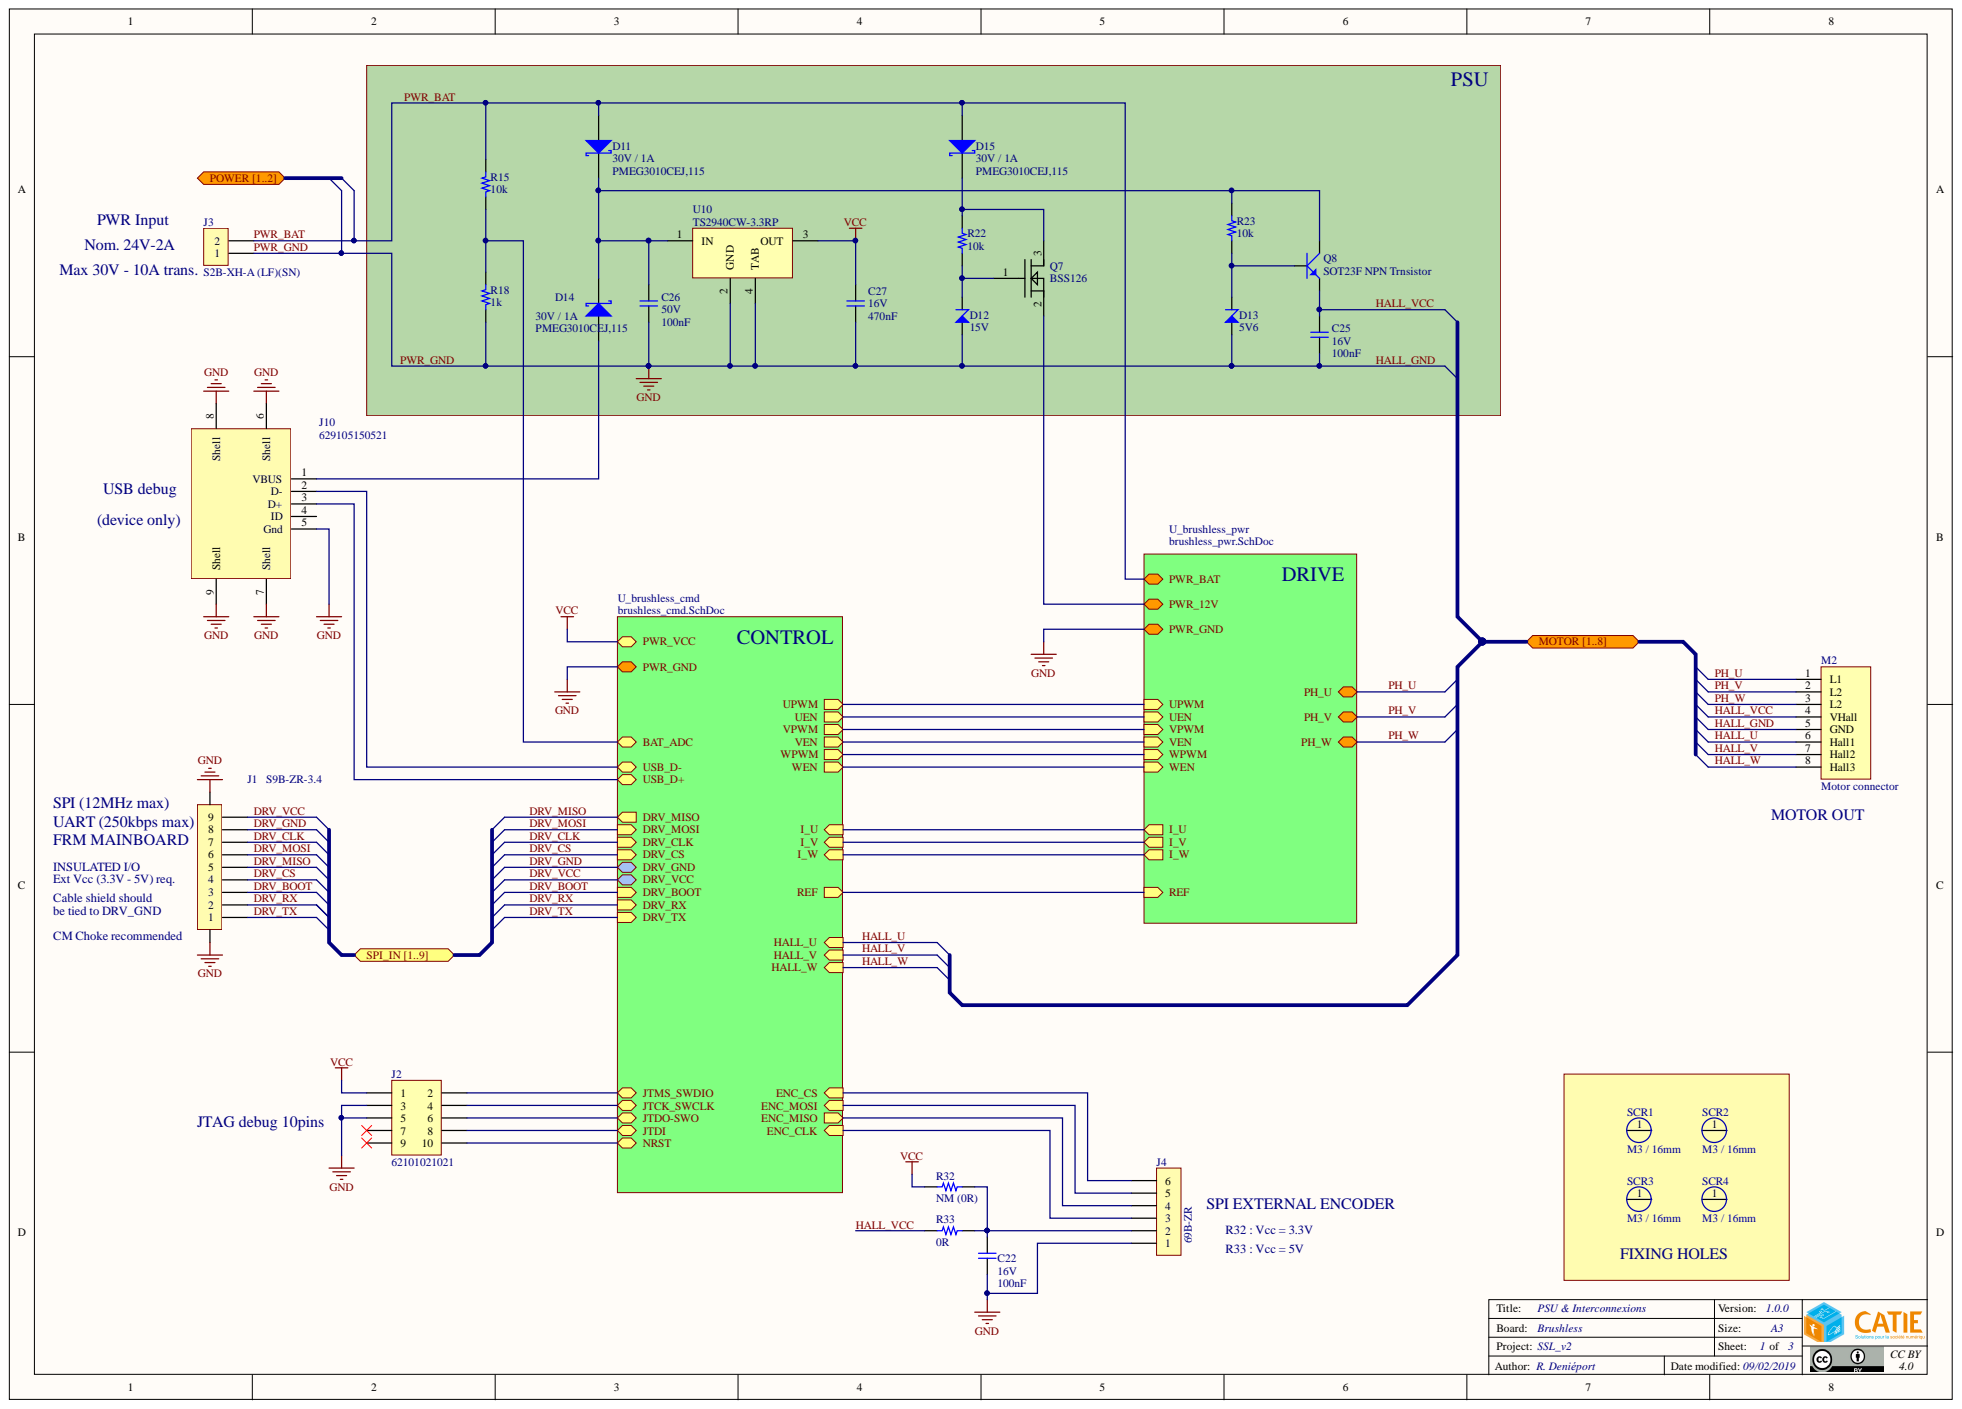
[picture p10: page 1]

SPI (12MHz max)
MOTOR OUT UART (250kbps max)
FRM MAINBOARD

INSULATED I/O
Ext Vcc (3.3V - 5V) req.
Cable shield should be tied to DRV_GND

Title: PSU & Interconnexions | Version: 1.0.0
Board: Brushless | Size: A3
Project: SSL_v2 | 1 3 Sheet: of

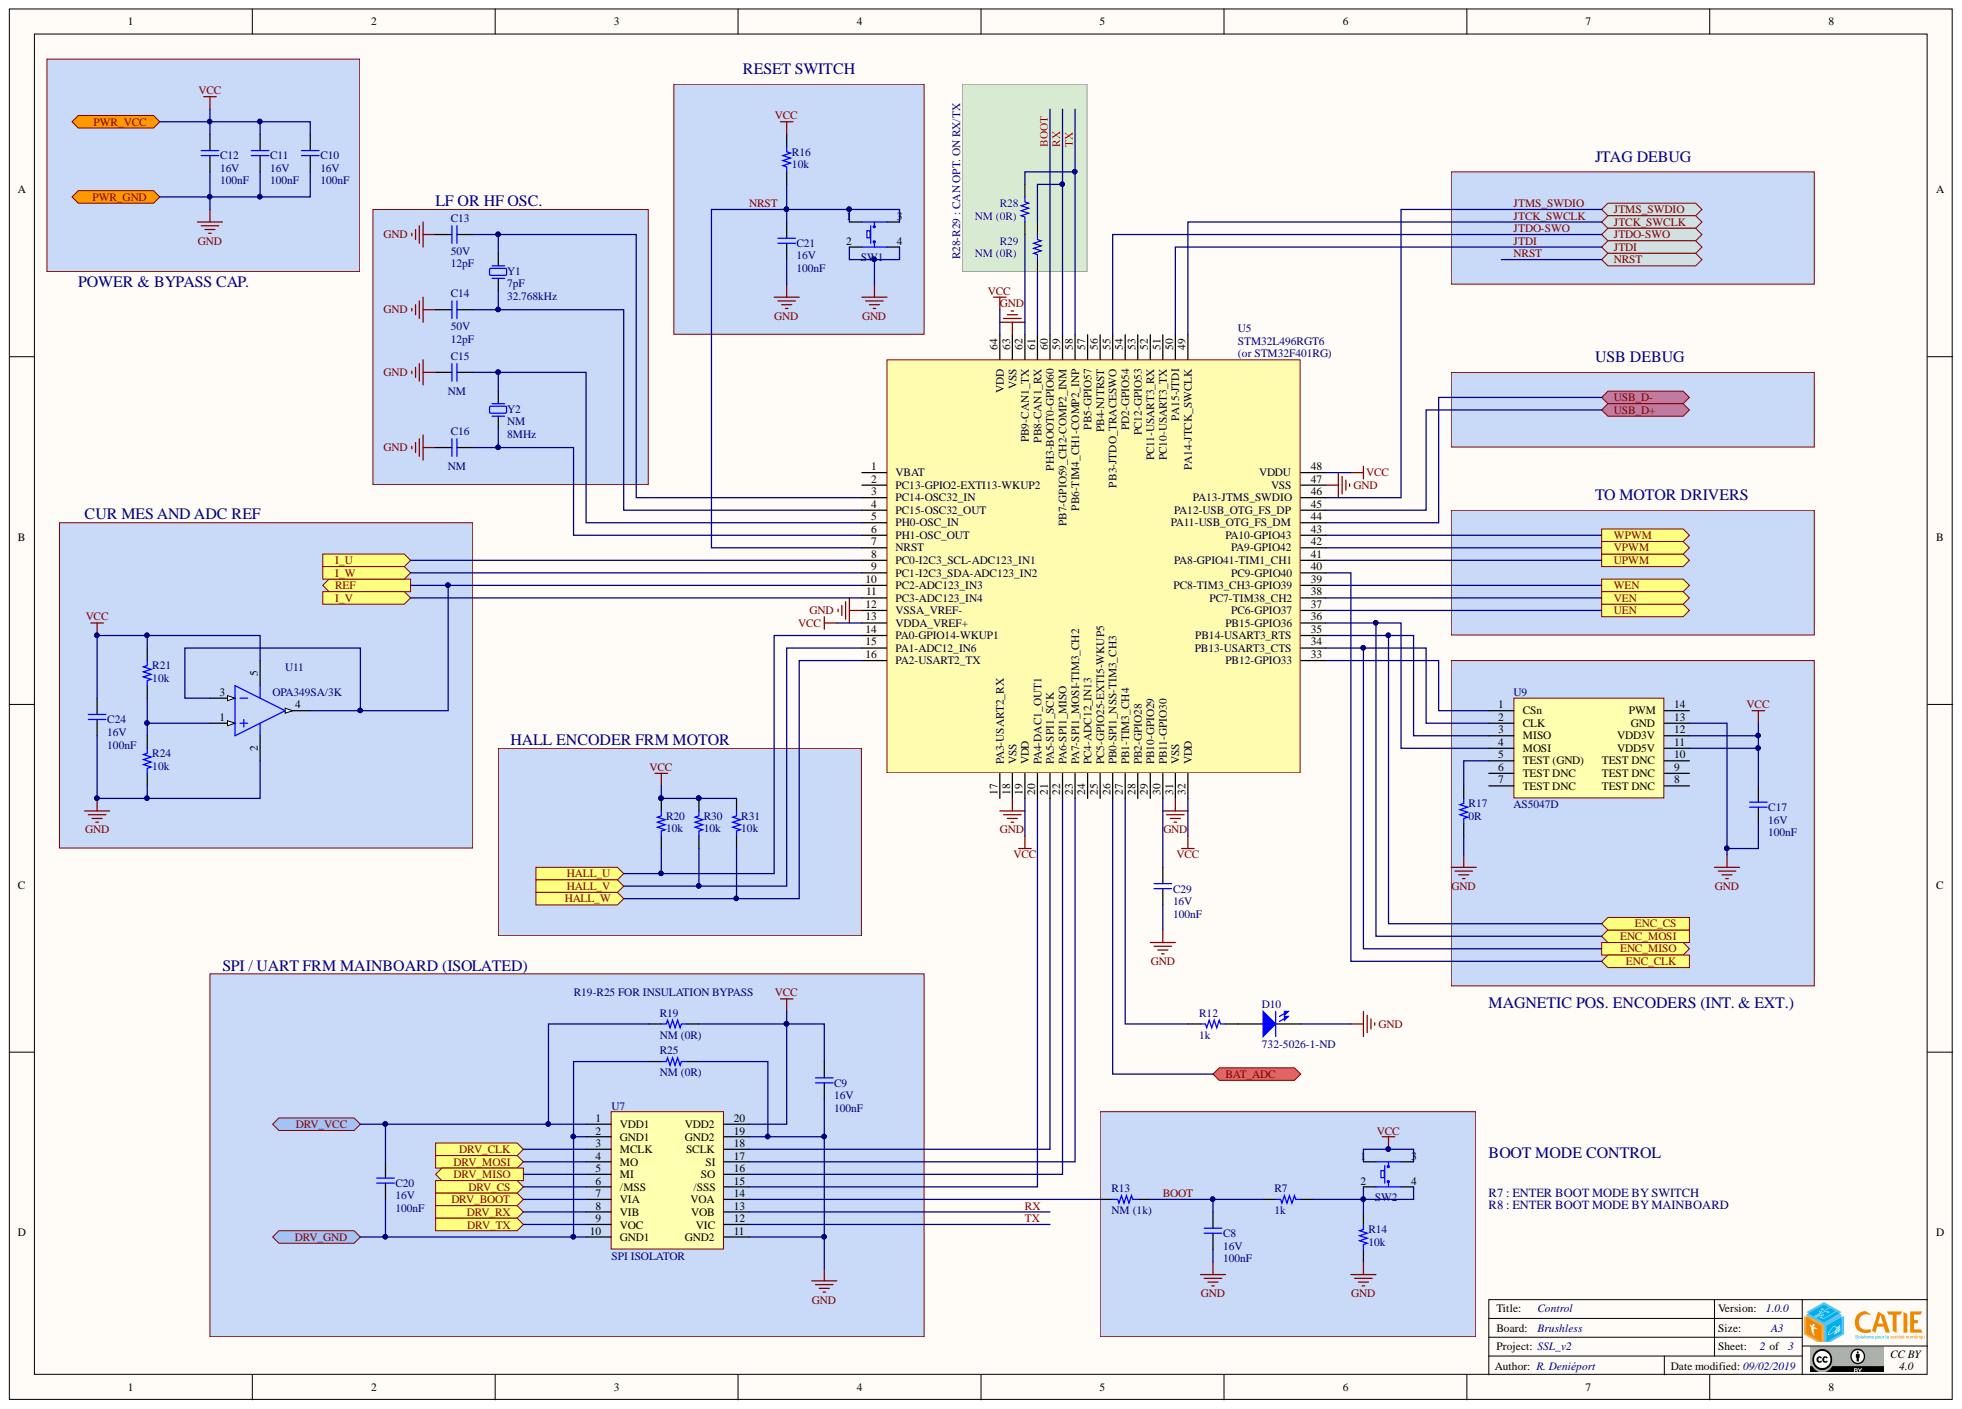
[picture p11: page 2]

R28-R29 : CAN OPT. ON RX/TX

LF OR HF OSC.

48 A14-JTCK_SWCLK 49 PA15-JTDI 50 PC10-USART3_TX 51 PC11-USART3_RX 52 PC12-GPIO53 53 PD2-GPIO54 54 PB3-JTDO_TRACESWO 55 PB4-NJTRST 56 PB5-GPIO57 57 PB6-TIM4_CH1-COMP2_INP 58 PB7-GPIO59_CH2-COMP2_INM 59 PH3-BOOT0-GPIO60 60 PB8-CAN1_RX 61 PB9-CAN1_TX 62 VSS 63 VDD 64

PC13-GPIO2-EXTI13-WKUP2 2 | GND

PC15-OSC32_OUT 4
PH0-OSC_IN 5 | WPWM VPWM UPWM

CUR MES AND ADC REF

PC3-ADC123_IN4 11
VSSA_VREF- 12

PA1-ADC12_IN6 15
PA2-USART2_TX 16

HALL ENCODER FRM MOTOR

VCC | TEST (GND) 5

SPI / UART FRM MAINBOARD (ISOLATED)

MAGNETIC POS. ENCODERS (INT. & EXT.)

RX
TX

R7 : ENTER BOOT MODE BY SWITCH R8 : ENTER BOOT MODE BY MAINBOARD

Title: Control | Version:
Board: Brushless | Size: A3
Project: SSL_v2 | 2 3 Sheet: of

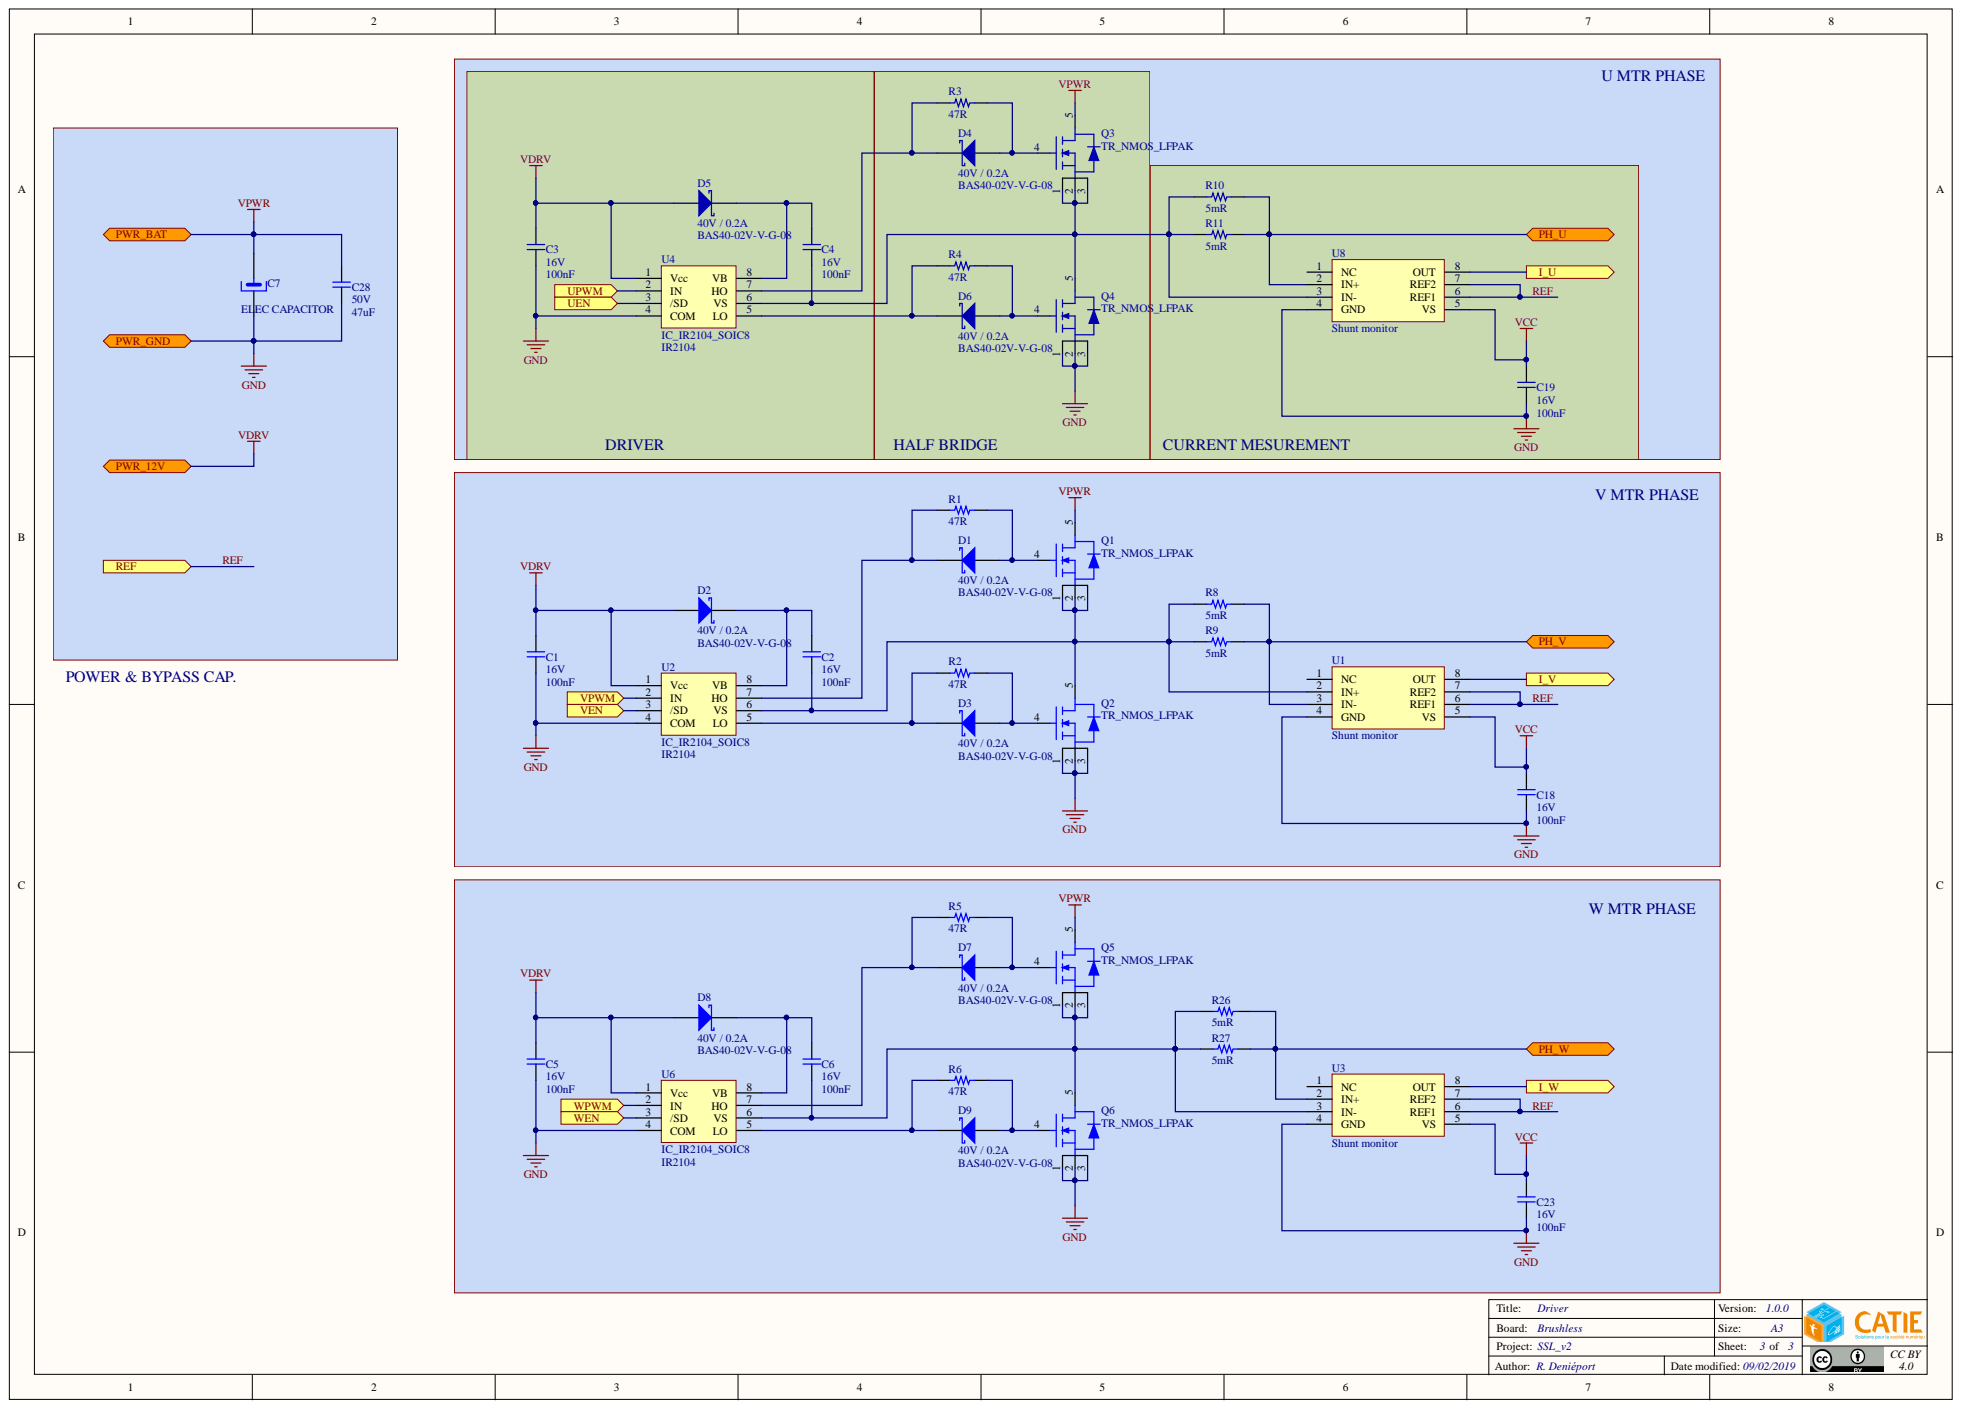
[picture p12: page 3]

Ti t le: D r iver | Size: Version:
Board: B rushles s | A
: SSL_v2 Project | Sheet : of
Author : R. Deni épor t | Date modi fied: 09/02/2019

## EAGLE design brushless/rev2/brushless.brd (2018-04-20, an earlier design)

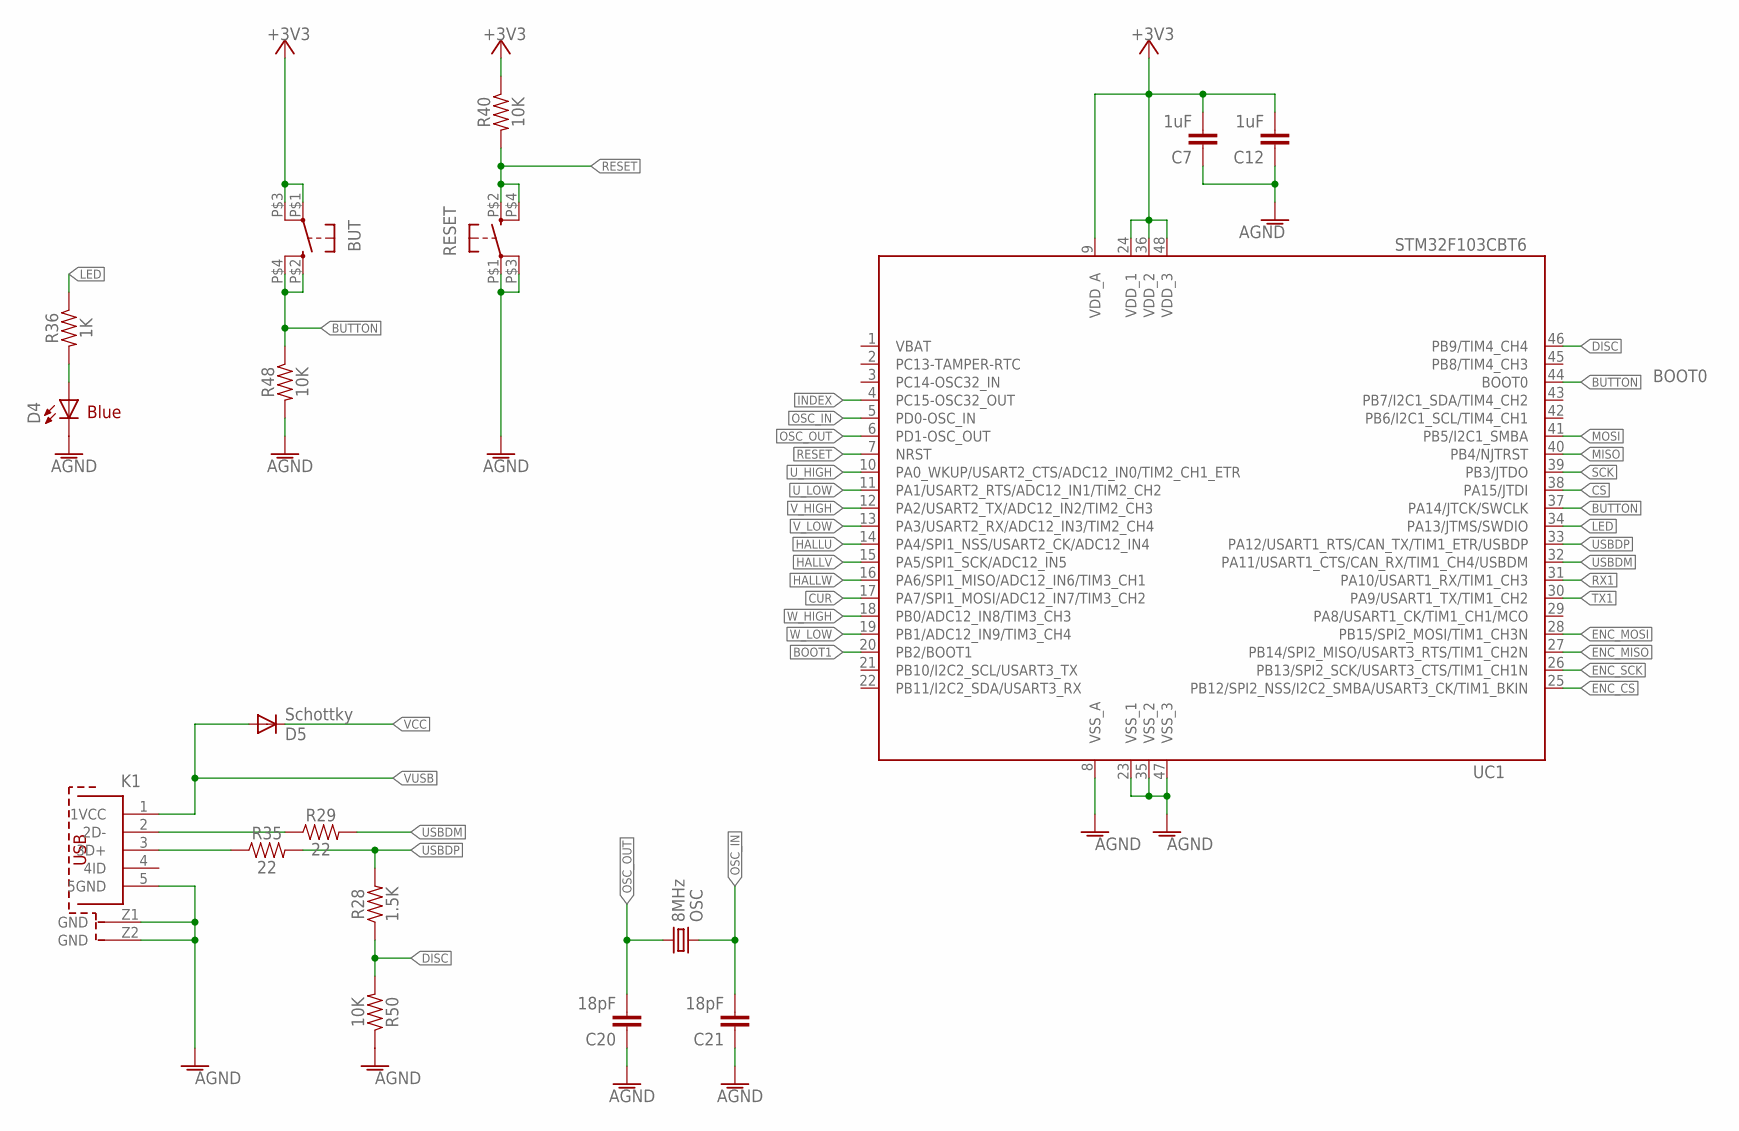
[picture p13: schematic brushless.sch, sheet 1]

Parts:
BUT: KMR211GLFS; PUSHBUTTON-KMR241GLFS; FARNELL 1437637
C7, C12: 1uF; 0805@1; FARNELL 2496946
C20, C21: 18pF; 0805@1; FARNELL 1414620
D4: Blue; LED-1206; FARNELL 1581233
D5: Schottky; SOD-323; FARNELL 8734593
K1: 614105150721; FARNELL 2470821
OSC: 8MHz; CRYSTAL-SMD-5X3; FARNELL 2467818
R28: 1.5K; 0805; FARNELL 2446909
R29, R35: 22; 0805; FARNELL 2446926
R36: 1K; 0805; FARNELL 2446904
R40, R48, R50: 10K; 0805; FARNELL 2447553
RESET: KMR211GLFS; PUSHBUTTON-KMR241GLFS; FARNELL 1437637
UC1: STM32F103CBT6; STM32_LQFP48; FARNELL 1606327

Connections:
+3V3: BUT.P$1 (1), BUT.P$3 (3), C7.2, C12.2, R40.1, UC1.9 (VDD_A), UC1.24 (VDD_1), UC1.36 (VDD_2), UC1.48 (VDD_3); also elsewhere on the board
AGND: C7.1, C12.1, C20.1, C21.1, D4.C, K1.5 (5GND), K1.Z1 (GND), K1.Z2 (GND), R48.2, R50.1, RESET.P$1 (1), RESET.P$3 (3), UC1.8 (VSS_A), UC1.23 (VSS_1), UC1.35 (VSS_2), UC1.47 (VSS_3); also elsewhere on the board
BOOT1: UC1.20 (PB2/BOOT1)
BUTTON: BUT.P$2 (2), BUT.P$4 (4), R48.1, UC1.37 (PA14/JTCK/SWCLK), UC1.44 (BOOT0)
CS: UC1.38 (PA15/JTDI); also elsewhere on the board
CUR: UC1.17 (PA7/SPI1_MOSI/ADC12_IN7/TIM3_CH2); also elsewhere on the board
DISC: R28.1, R50.2, UC1.46 (PB9/TIM4_CH4)
ENC_CS: UC1.25 (PB12/SPI2_NSS/I2C2_SMBA/USART3_CK/TIM1_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); also elsewhere on the board
ENC_MISO: UC1.27 (PB14/SPI2_MISO/USART3_RTS/TIM1_CH2N); also elsewhere on the board
ENC_MOSI: UC1.28 (PB15/SPI2_MOSI/TIM1_CH3N); also elsewhere on the board
ENC_SCK: UC1.26 (PB13/SPI2_SCK/USART3_CTS/TIM1_CH1N); also elsewhere on the board
HALLU: UC1.14 (PA4/SPI1_NSS/USART2_CK/ADC12_IN4); also elsewhere on the board
HALLV: UC1.15 (PA5/SPI1_SCK/ADC12_IN5); also elsewhere on the board
HALLW: UC1.16 (PA6/SPI1_MISO/ADC12_IN6/TIM3_CH1); also elsewhere on the board
INDEX: UC1.4 (PC15-OSC32_OUT)
LED: R36.1, UC1.34 (PA13/JTMS/SWDIO)
MISO: UC1.40 (PB4/NJTRST); also elsewhere on the board
MOSI: UC1.41 (PB5/I2C1_SMBA); also elsewhere on the board
unnamed: D4.A, R36.2
unnamed: K1.2 (2D-), R29.1
unnamed: K1.3 (3D+), R35.1
OSC_IN: C21.2, OSC.3 (2), UC1.5 (PD0-OSC_IN)
OSC_OUT: C20.2, OSC.1, UC1.6 (PD1-OSC_OUT)
RESET: R40.2, RESET.P$2 (2), RESET.P$4 (4), UC1.7 (NRST)
RX1: UC1.31 (PA10/USART1_RX/TIM1_CH3)
SCK: UC1.39 (PB3/JTDO); also elsewhere on the board
TX1: UC1.30 (PA9/USART1_TX/TIM1_CH2)
USBDM: R29.2, UC1.32 (PA11/USART1_CTS/CAN_RX/TIM1_CH4/USBDM)
USBDP: R28.2, R35.2, UC1.33 (PA12/USART1_RTS/CAN_TX/TIM1_ETR/USBDP)
U_HIGH: UC1.10 (PA0_WKUP/USART2_CTS/ADC12_IN0/TIM2_CH1_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); also elsewhere on the board
U_LOW: UC1.11 (PA1/USART2_RTS/ADC12_IN1/TIM2_CH2); also elsewhere on the board
VBAT: UC1.1 (VBAT)
VCC: D5.1 (C); also elsewhere on the board
VUSB: D5.2 (A), K1.1 (1VCC); also elsewhere on the board
V_HIGH: UC1.12 (PA2/USART2_TX/ADC12_IN2/TIM2_CH3); also elsewhere on the board
V_LOW: UC1.13 (PA3/USART2_RX/ADC12_IN3/TIM2_CH4); also elsewhere on the board
W_HIGH: UC1.18 (PB0/ADC12_IN8/TIM3_CH3); also elsewhere on the board
W_LOW: UC1.19 (PB1/ADC12_IN9/TIM3_CH4); also elsewhere on the board

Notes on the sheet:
BOOT0
Blue

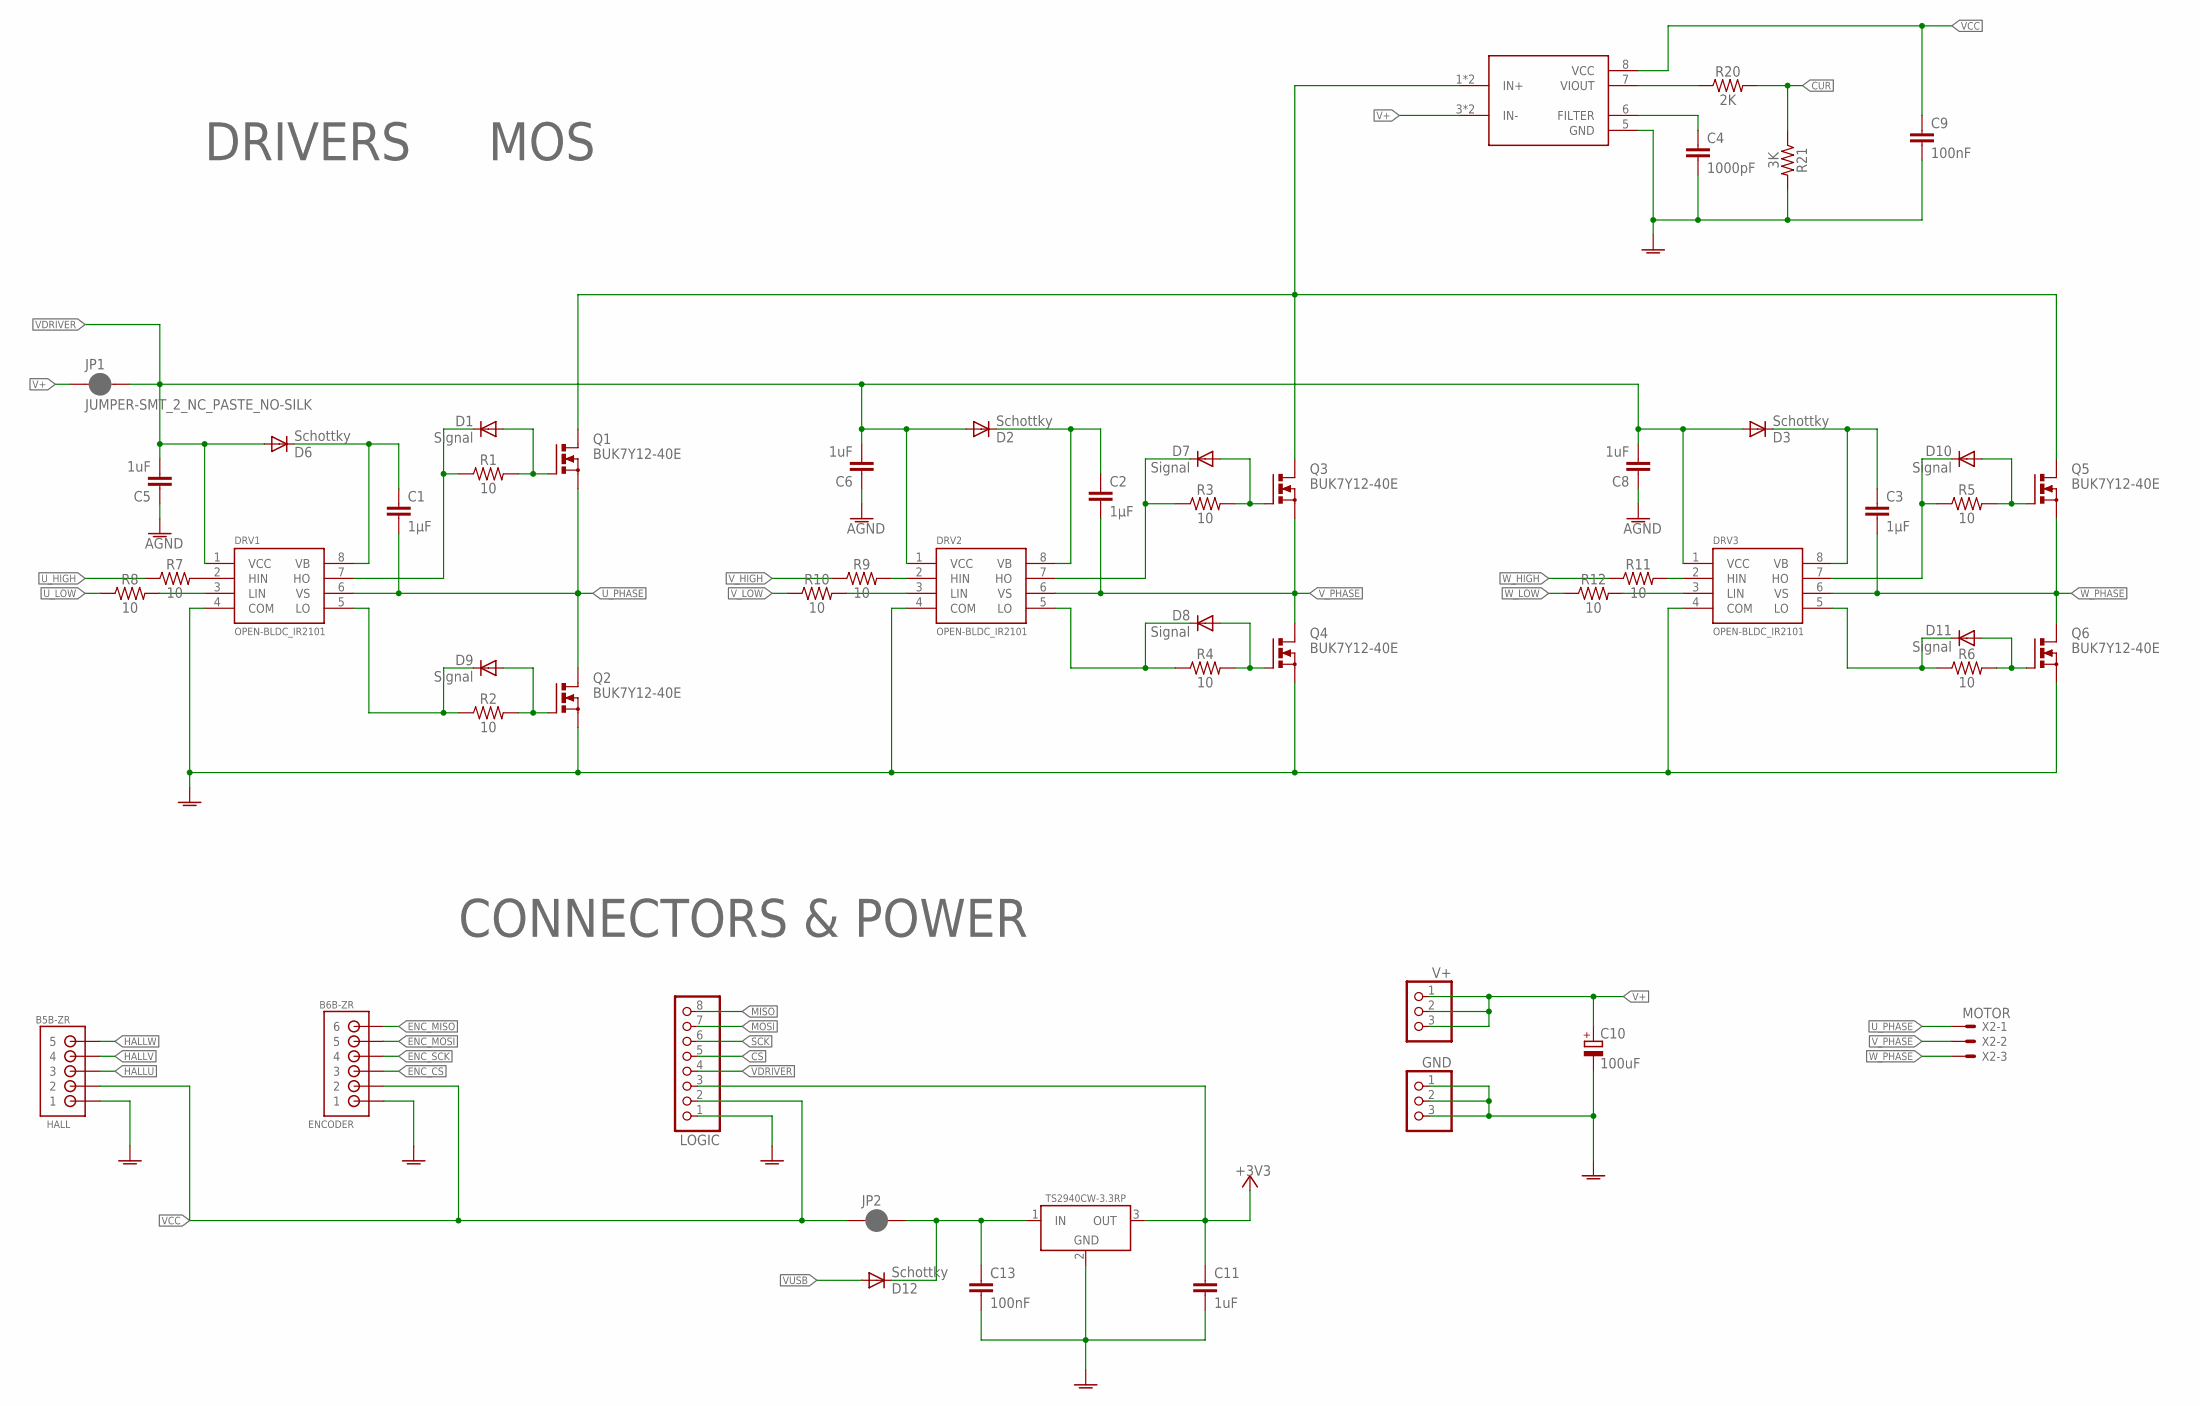
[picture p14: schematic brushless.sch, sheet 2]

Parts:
C1, C2, C3: 1µF; 0805; FARNELL 2496946
C4: 1000pF; 0805@1; FARNELL 2392334
C5, C6, C8, C11: 1uF; 0805@1; FARNELL 2496946
C9, C13: 100nF; 0805@1; FARNELL 1759143RL
C10: 100uF; E3,5-8; FARNELL 1870964
D1, D7, D8, D9, D10, D11: Signal; SOD-323; FARNELL 1843678RL
D2, D3, D6, D12: Schottky; SOD-323; FARNELL 8734593
DRV1, DRV2, DRV3: OPEN-BLDC_IR2101; OPEN-BLDC_SO-8; FARNELL 8638756
ENCODER: B6B-ZR
GND: CONNEC_1X03; FARNELL 1022248
HALL: B5B-ZR
JP1, JP2: JUMPER-SMT_2_NC_PASTE_NO-SILK; SMT-JUMPER_2_NC_PASTE_NO-SILK
LOGIC: CONNEC_1X08; FARNELL 1022256
Q1, Q2, Q3, Q4, Q5, Q6: BUK7Y12-40E; SOT669; FARNELL 2319916
R1, R2, R3, R4, R5, R6, R7, R8, R9, R10, R11, R12: 10; 0805; FARNELL 2498048
R20: 2K; 0805; FARNELL 2446939
R21: 3K; 0805; FARNELL 2446965
REG1: TS2940CW-3.3RP; SOT223; FARNELL 7261403
SENSE: ACS712; SO8; FARNELL 1329624
V+: CONNEC_1X03; FARNELL 1022248
X2: MOTOR; JST-XH-03-PACKAGE-LONG-PAD

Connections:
+3V3: C11.1, LOGIC.3, REG1.3 (OUT); also elsewhere on the board
AGND: C4.2, C5.1, C6.1, C8.1, C9.2, C10.-, C11.2, C13.2, DRV1.4 (COM), DRV2.4 (COM), DRV3.4 (COM), ENCODER.1, GND.1, GND.2, GND.3, HALL.1, LOGIC.1, Q2.1 (S), Q2.2 (S), Q2.3 (S), Q4.1 (S), Q4.2 (S), Q4.3 (S), Q6.1 (S), Q6.2 (S), Q6.3 (S), R21.2, REG1.2 (GND), SENSE.5 (GND); also elsewhere on the board
CS: LOGIC.5; also elsewhere on the board
CUR: R20.2, R21.1; also elsewhere on the board
ENC_CS: ENCODER.3; also elsewhere on the board
ENC_MISO: ENCODER.6; also elsewhere on the board
ENC_MOSI: ENCODER.5; also elsewhere on the board
ENC_SCK: ENCODER.4; also elsewhere on the board
HALLU: HALL.3; also elsewhere on the board
HALLV: HALL.4; also elsewhere on the board
HALLW: HALL.5; also elsewhere on the board
MISO: LOGIC.8; also elsewhere on the board
MOSI: LOGIC.7; also elsewhere on the board
unnamed: D7.2 (A), Q3.4 (G), R3.2
unnamed: D9.2 (A), Q2.4 (G), R2.2
unnamed: DRV1.2 (HIN), R7.2
unnamed: C1.1, D6.1 (C), DRV1.8 (VB)
unnamed: D8.2 (A), Q4.4 (G), R4.2
unnamed: D10.2 (A), Q5.4 (G), R5.2
unnamed: DRV1.3 (LIN), R8.2
unnamed: D11.2 (A), Q6.4 (G), R6.2
unnamed: C2.1, D2.1 (C), DRV2.8 (VB)
unnamed: D1.2 (A), Q1.4 (G), R1.2
unnamed: D10.1 (C), DRV3.7 (HO), R5.1
unnamed: D11.1 (C), DRV3.5 (LO), R6.1
unnamed: DRV2.3 (LIN), R10.2
unnamed: C3.1, D3.1 (C), DRV3.8 (VB)
unnamed: DRV2.2 (HIN), R9.2
unnamed: DRV3.2 (HIN), R11.2
unnamed: DRV3.3 (LIN), R12.2
unnamed: C13.1, D12.1 (C), JP2.2, REG1.1 (IN)
unnamed: R20.1, SENSE.7 (VIOUT)
unnamed: C4.1, SENSE.6 (FILTER)
SCK: LOGIC.6; also elsewhere on the board
U_GATE_HIGH: D1.1 (C), DRV1.7 (HO), R1.1
U_GATE_LOW: D9.1 (C), DRV1.5 (LO), R2.1
U_HIGH: R7.1; also elsewhere on the board
U_LOW: R8.1; also elsewhere on the board
U_PHASE: C1.2, DRV1.6 (VS), Q1.1 (S), Q1.2 (S), Q1.3 (S), Q2.MB (D), X2.1
V+: C10.+, JP1.1, SENSE.3 (IN-), SENSE.4 (IN-), V+.1, V+.2, V+.3
V+_MOS: Q1.MB (D), Q3.MB (D), Q5.MB (D), SENSE.1 (IN+), SENSE.2 (IN+)
VCC: C9.1, ENCODER.2, HALL.2, JP2.1, LOGIC.2, SENSE.8 (VCC); also elsewhere on the board
VDRIVER: C5.2, C6.2, C8.2, D2.2 (A), D3.2 (A), D6.2 (A), DRV1.1 (VCC), DRV2.1 (VCC), DRV3.1 (VCC), JP1.2, LOGIC.4
VUSB: D12.2 (A); also elsewhere on the board
V_GATE_HIGH: D7.1 (C), DRV2.7 (HO), R3.1
V_GATE_LOW: D8.1 (C), DRV2.5 (LO), R4.1
V_HIGH: R9.1; also elsewhere on the board
V_LOW: R10.1; also elsewhere on the board
V_PHASE: C2.2, DRV2.6 (VS), Q3.1 (S), Q3.2 (S), Q3.3 (S), Q4.MB (D), X2.2
W_HIGH: R11.1; also elsewhere on the board
W_LOW: R12.1; also elsewhere on the board
W_PHASE: C3.2, DRV3.6 (VS), Q5.1 (S), Q5.2 (S), Q5.3 (S), Q6.MB (D), X2.3

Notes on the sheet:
MOS
DRIVERS
CONNECTORS & POWER

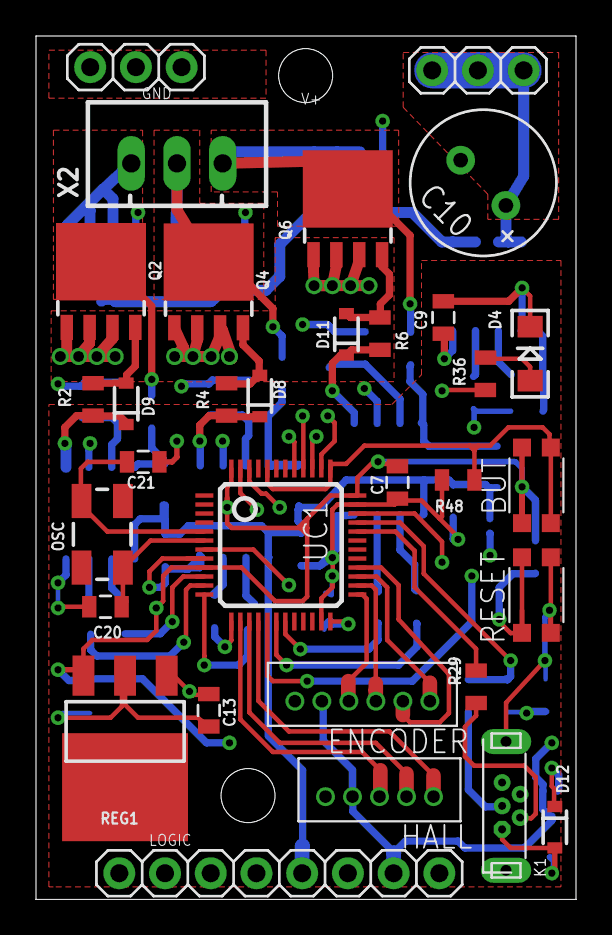
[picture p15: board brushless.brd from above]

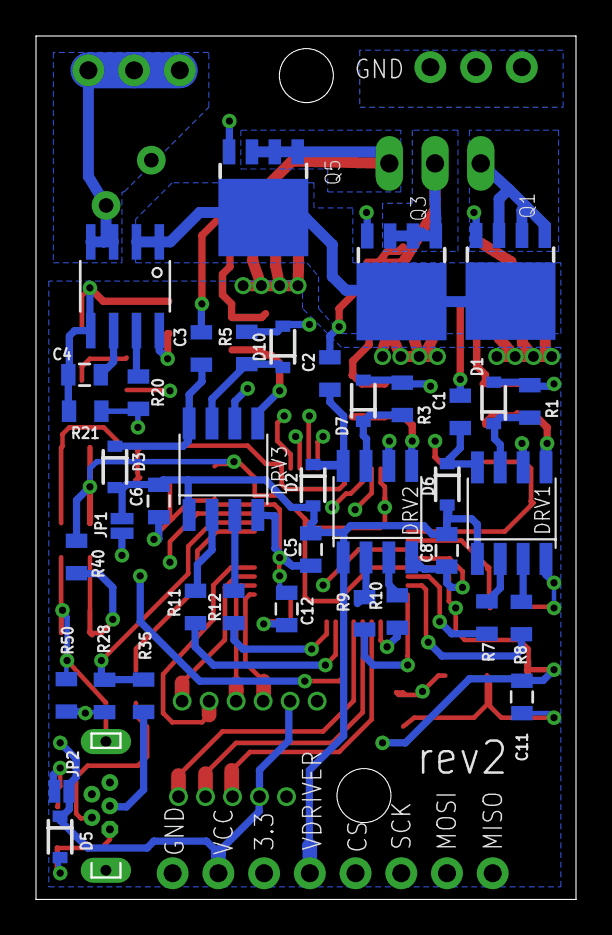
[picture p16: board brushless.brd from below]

Board: 4 copper layers, 30.0 x 48.0 mm, 72 parts (40 on the bottom side), 63 nets.

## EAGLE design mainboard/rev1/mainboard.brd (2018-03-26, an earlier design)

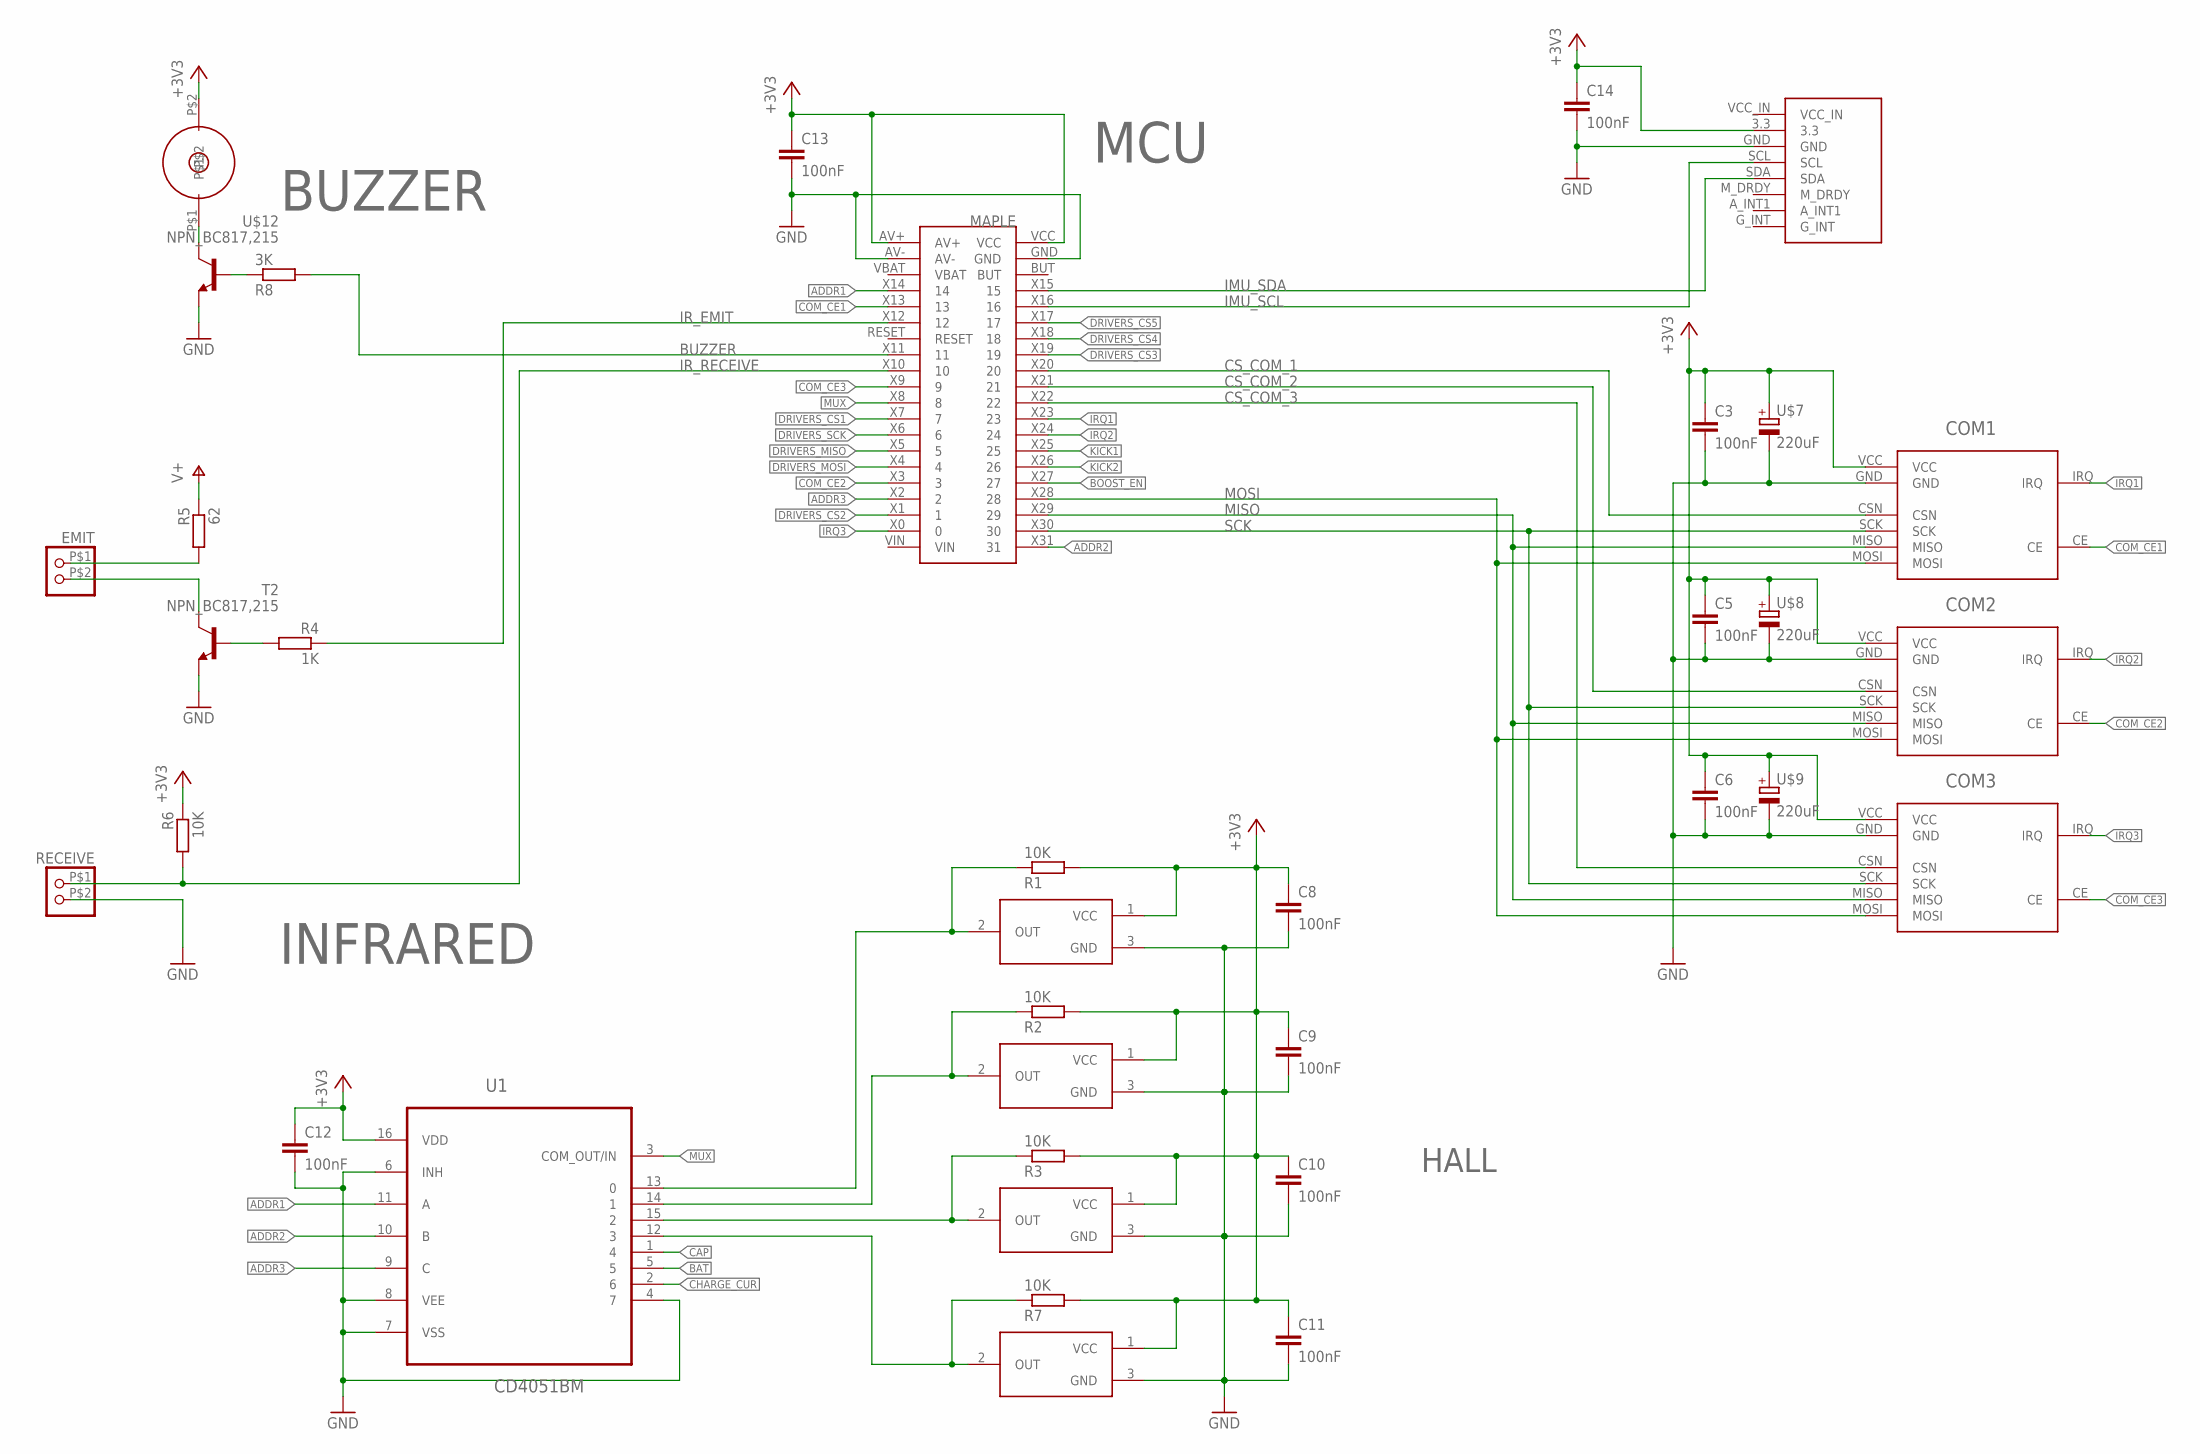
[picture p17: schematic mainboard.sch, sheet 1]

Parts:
C3, C5, C6, C8, C9, C10, C11, C12, C13, C14: 100nF; 0805@1; FARNELL 2496946
COM1, COM2, COM3: NRF24L01; FARNELL 1668343
EMIT: CONNEC_1X02JST-ZH; JST_ZH_2P; FARNELL 1212763
MAPLE: MAPLE_MINI; CONNEC_2X20; FARNELL 1593469,1593469
R1, R2, R3, R6, R7: 10K; R0805; FARNELL 2447553
R4: 1K; R0805; FARNELL 2446904
R5: 62; R0805; FARNELL 2138819
R8: 3K; R0805; FARNELL 2446965
RECEIVE: CONNEC_1X02JST-ZH; JST_ZH_2P; FARNELL 3152856
T2: NPN_BC817,215; SOT-23; FARNELL 1081223
U1: CD4051BM; SOIC127P600X175-16N; FARNELL 2334931
U$1, U$5, U$10, U$11: DRV5023FAEDBZRQ1; SOT-23; FARNELL 2673327RL
U$2: GY-85; FARNELL 1593463
U$7, U$8, U$9: 220uF; PANASONIC_D8; FARNELL 1850103
U$12: NPN_BC817,215; SOT-23; FARNELL 1081223
U$13: BUZZER66

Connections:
+3V3: C3.1, C5.1, C6.1, C8.1, C9.1, C10.1, C11.1, C12.1, C13.1, C14.1, COM1.VCC, COM2.VCC, COM3.VCC, MAPLE.AV+, MAPLE.VCC, R1.2, R2.2, R3.2, R6.1, R7.2, U1.16 (VDD), U$1.1 (VCC), U$2.3.3, U$5.1 (VCC), U$7.+, U$8.+, U$9.+, U$10.1 (VCC), U$11.1 (VCC), U$13.P$2; also elsewhere on the board
ADDR1: MAPLE.X14 (14), U1.11 (A)
ADDR2: MAPLE.X31 (31), U1.10 (B)
ADDR3: MAPLE.X2 (2), U1.9 (C)
BAT: U1.5; also elsewhere on the board
BOOST_EN: MAPLE.X27 (27); also elsewhere on the board
BUZZER: MAPLE.X11 (11), R8.2
CAP: U1.1 (4); also elsewhere on the board
CHARGE_CUR: U1.2 (6); also elsewhere on the board
COM_CE1: COM1.CE, MAPLE.X13 (13)
COM_CE2: COM2.CE, MAPLE.X3 (3)
COM_CE3: COM3.CE, MAPLE.X9 (9)
CS_COM_1: COM1.CSN, MAPLE.X20 (20)
CS_COM_2: COM2.CSN, MAPLE.X21 (21)
CS_COM_3: COM3.CSN, MAPLE.X22 (22)
DRIVERS_CS1: MAPLE.X7 (7); also elsewhere on the board
DRIVERS_CS2: MAPLE.X1 (1); also elsewhere on the board
DRIVERS_CS3: MAPLE.X19 (19); also elsewhere on the board
DRIVERS_CS4: MAPLE.X18 (18); also elsewhere on the board
DRIVERS_CS5: MAPLE.X17 (17); also elsewhere on the board
DRIVERS_MISO: MAPLE.X5 (5); also elsewhere on the board
DRIVERS_MOSI: MAPLE.X4 (4); also elsewhere on the board
DRIVERS_SCK: MAPLE.X6 (6); also elsewhere on the board
GND: C3.2, C5.2, C6.2, C8.2, C9.2, C10.2, C11.2, C12.2, C13.2, C14.2, COM1.GND, COM2.GND, COM3.GND, MAPLE.AV-, MAPLE.GND, RECEIVE.P$2 (2), T2.2 (E), U1.4 (7), U1.6 (INH), U1.7 (VSS), U1.8 (VEE), U$1.3 (GND), U$2.GND, U$5.3 (GND), U$7.-, U$8.-, U$9.-, U$10.3 (GND), U$11.3 (GND), U$12.2 (E); also elsewhere on the board
HALL1: R1.1, U1.13 (0), U$1.2 (OUT)
HALL2: R2.1, U1.14 (1), U$5.2 (OUT)
HALL3: R3.1, U1.15 (2), U$10.2 (OUT)
HALL4: R7.1, U1.12 (3), U$11.2 (OUT)
IMU_SCL: MAPLE.X16 (16), U$2.SCL
IMU_SDA: MAPLE.X15 (15), U$2.SDA
IRQ1: COM1.IRQ, MAPLE.X23 (23)
IRQ2: COM2.IRQ, MAPLE.X24 (24)
IRQ3: COM3.IRQ, MAPLE.X0 (0)
IR_EMIT: MAPLE.X12 (12), R4.1
IR_RECEIVE: MAPLE.X10 (10), R6.2, RECEIVE.P$1 (1)
KICK1: MAPLE.X25 (25); also elsewhere on the board
KICK2: MAPLE.X26 (26); also elsewhere on the board
MISO: COM1.MISO, COM2.MISO, COM3.MISO, MAPLE.X29 (29)
MOSI: COM1.MOSI, COM2.MOSI, COM3.MOSI, MAPLE.X28 (28)
MUX: MAPLE.X8 (8), U1.3 (COM_OUT/IN)
unnamed: R8.1, U$12.1 (B)
unnamed: U$12.3 (C), U$13.P$1
unnamed: EMIT.P$1 (1), R5.2
unnamed: EMIT.P$2 (2), T2.3 (C)
unnamed: R4.2, T2.1 (B)
SCK: COM1.SCK, COM2.SCK, COM3.SCK, MAPLE.X30 (30)
V+: R5.1; also elsewhere on the board

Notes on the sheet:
MCU
BUZZER
INFRARED
HALL

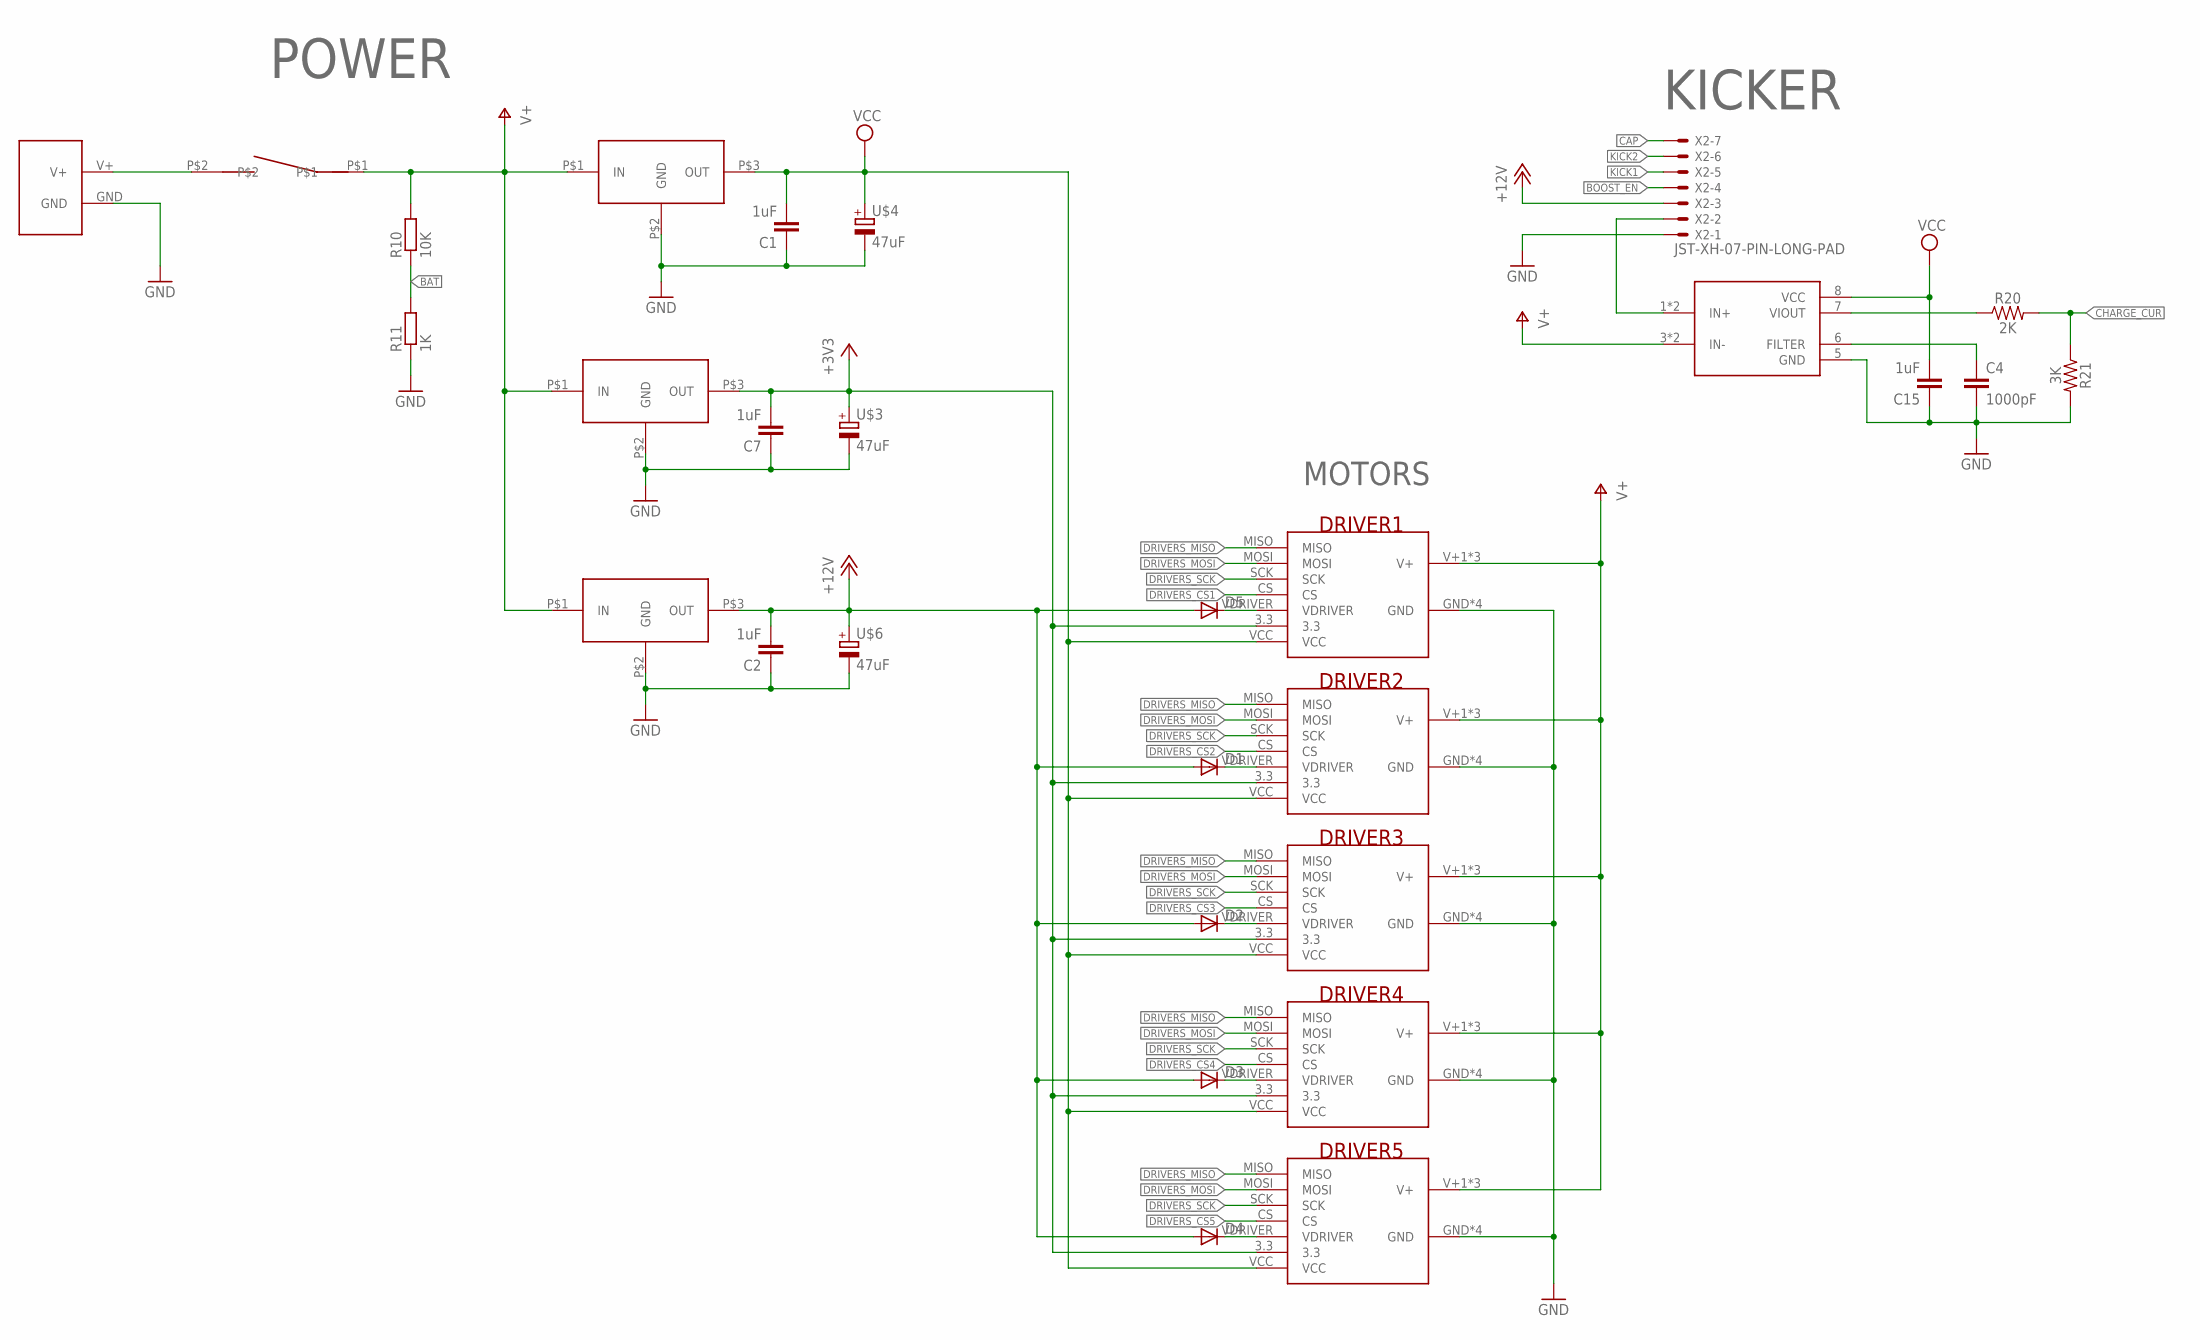
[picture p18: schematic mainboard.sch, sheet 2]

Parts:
C1, C2, C7, C15: 1uF; 0805@1; FARNELL 2496946
C4: 1000pF; 0805@1; FARNELL 2496935
D1, D2, D3, D4, D5: DIODESOD; SOD-323; FARNELL 8737843RL
DRIVER1, DRIVER2, DRIVER3, DRIVER4, DRIVER5: RHOBAN_BL_DRIVER; FARNELL 1593459,1593459,1593463
R10: 10K; R0805; FARNELL 2447553
R11: 1K; R0805; FARNELL 2446904
R20: 2K; 0805; FARNELL 2446939
R21: 3K; 0805; FARNELL 2446965
REG3.3V: REG_5V; TRACOPOWER; FARNELL 1696319
REG3.3V1: REG_5V; TRACOPOWER; FARNELL 1672130
REG5V: REG_5V; TRACOPOWER; FARNELL 1696320
SENSE: ACS712; SO8; FARNELL 1329623
U$3, U$4, U$6: 47uF; PANASONIC_D; FARNELL 9696946
U$15: SRB22A2FBBNN; FARNELL 1383947
X2: JST-XH-07-PIN-LONG-PAD; JST-XH-07-PACKAGE-LONG-PAD
XT60: CONNEC_ALIM; XT60

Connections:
+3V3: C7.2, DRIVER1.3.3, DRIVER2.3.3, DRIVER3.3.3, DRIVER4.3.3, DRIVER5.3.3, REG3.3V.P$3 (OUT), U$3.+; also elsewhere on the board
+12V: C2.2, D1.2 (A), D2.2 (A), D3.2 (A), D4.2 (A), D5.2 (A), REG3.3V1.P$3 (OUT), U$6.+, X2.3
BAT: R10.1, R11.2; also elsewhere on the board
BOOST_EN: X2.4; also elsewhere on the board
CAP: X2.7; also elsewhere on the board
CHARGE_CUR: R20.2, R21.1; also elsewhere on the board
DRIVERS_CS1: DRIVER1.CS; also elsewhere on the board
DRIVERS_CS2: DRIVER2.CS; also elsewhere on the board
DRIVERS_CS3: DRIVER3.CS; also elsewhere on the board
DRIVERS_CS4: DRIVER4.CS; also elsewhere on the board
DRIVERS_CS5: DRIVER5.CS; also elsewhere on the board
DRIVERS_MISO: DRIVER1.MISO, DRIVER2.MISO, DRIVER3.MISO, DRIVER4.MISO, DRIVER5.MISO; also elsewhere on the board
DRIVERS_MOSI: DRIVER1.MOSI, DRIVER2.MOSI, DRIVER3.MOSI, DRIVER4.MOSI, DRIVER5.MOSI; also elsewhere on the board
DRIVERS_SCK: DRIVER1.SCK, DRIVER2.SCK, DRIVER3.SCK, DRIVER4.SCK, DRIVER5.SCK; also elsewhere on the board
GND: C1.1, C2.1, C4.2, C7.1, C15.1, DRIVER1.GND, DRIVER1.GND2 (GND), DRIVER1.GND3 (GND), DRIVER1.GND4 (GND), DRIVER2.GND, DRIVER2.GND2 (GND), DRIVER2.GND3 (GND), DRIVER2.GND4 (GND), DRIVER3.GND, DRIVER3.GND2 (GND), DRIVER3.GND3 (GND), DRIVER3.GND4 (GND), DRIVER4.GND, DRIVER4.GND2 (GND), DRIVER4.GND3 (GND), DRIVER4.GND4 (GND), DRIVER5.GND, DRIVER5.GND2 (GND), DRIVER5.GND3 (GND), DRIVER5.GND4 (GND), R11.1, R21.2, REG3.3V.P$2 (GND), REG3.3V1.P$2 (GND), REG5V.P$2 (GND), SENSE.5 (GND), U$3.-, U$4.-, U$6.-, X2.1, XT60.GND; also elsewhere on the board
KICK1: X2.5; also elsewhere on the board
KICK2: X2.6; also elsewhere on the board
unnamed: U$15.P$2, XT60.V+
unnamed: C4.1, SENSE.6 (FILTER)
unnamed: SENSE.1 (IN+), SENSE.2 (IN+), X2.2
unnamed: D5.1 (C), DRIVER1.VDRIVER
unnamed: D3.1 (C), DRIVER4.VDRIVER
unnamed: D4.1 (C), DRIVER5.VDRIVER
unnamed: D2.1 (C), DRIVER3.VDRIVER
unnamed: D1.1 (C), DRIVER2.VDRIVER
unnamed: R20.1, SENSE.7 (VIOUT)
V+: DRIVER1.V+1 (V+), DRIVER1.V+2 (V+), DRIVER1.V+3 (V+), DRIVER2.V+1 (V+), DRIVER2.V+2 (V+), DRIVER2.V+3 (V+), DRIVER3.V+1 (V+), DRIVER3.V+2 (V+), DRIVER3.V+3 (V+), DRIVER4.V+1 (V+), DRIVER4.V+2 (V+), DRIVER4.V+3 (V+), DRIVER5.V+1 (V+), DRIVER5.V+2 (V+), DRIVER5.V+3 (V+), R10.2, REG3.3V.P$1 (IN), REG3.3V1.P$1 (IN), REG5V.P$1 (IN), SENSE.3 (IN-), SENSE.4 (IN-), U$15.P$1; also elsewhere on the board
VCC: C1.2, C15.2, DRIVER1.VCC, DRIVER2.VCC, DRIVER3.VCC, DRIVER4.VCC, DRIVER5.VCC, REG5V.P$3 (OUT), SENSE.8 (VCC), U$4.+

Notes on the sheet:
POWER
KICKER
MOTORS

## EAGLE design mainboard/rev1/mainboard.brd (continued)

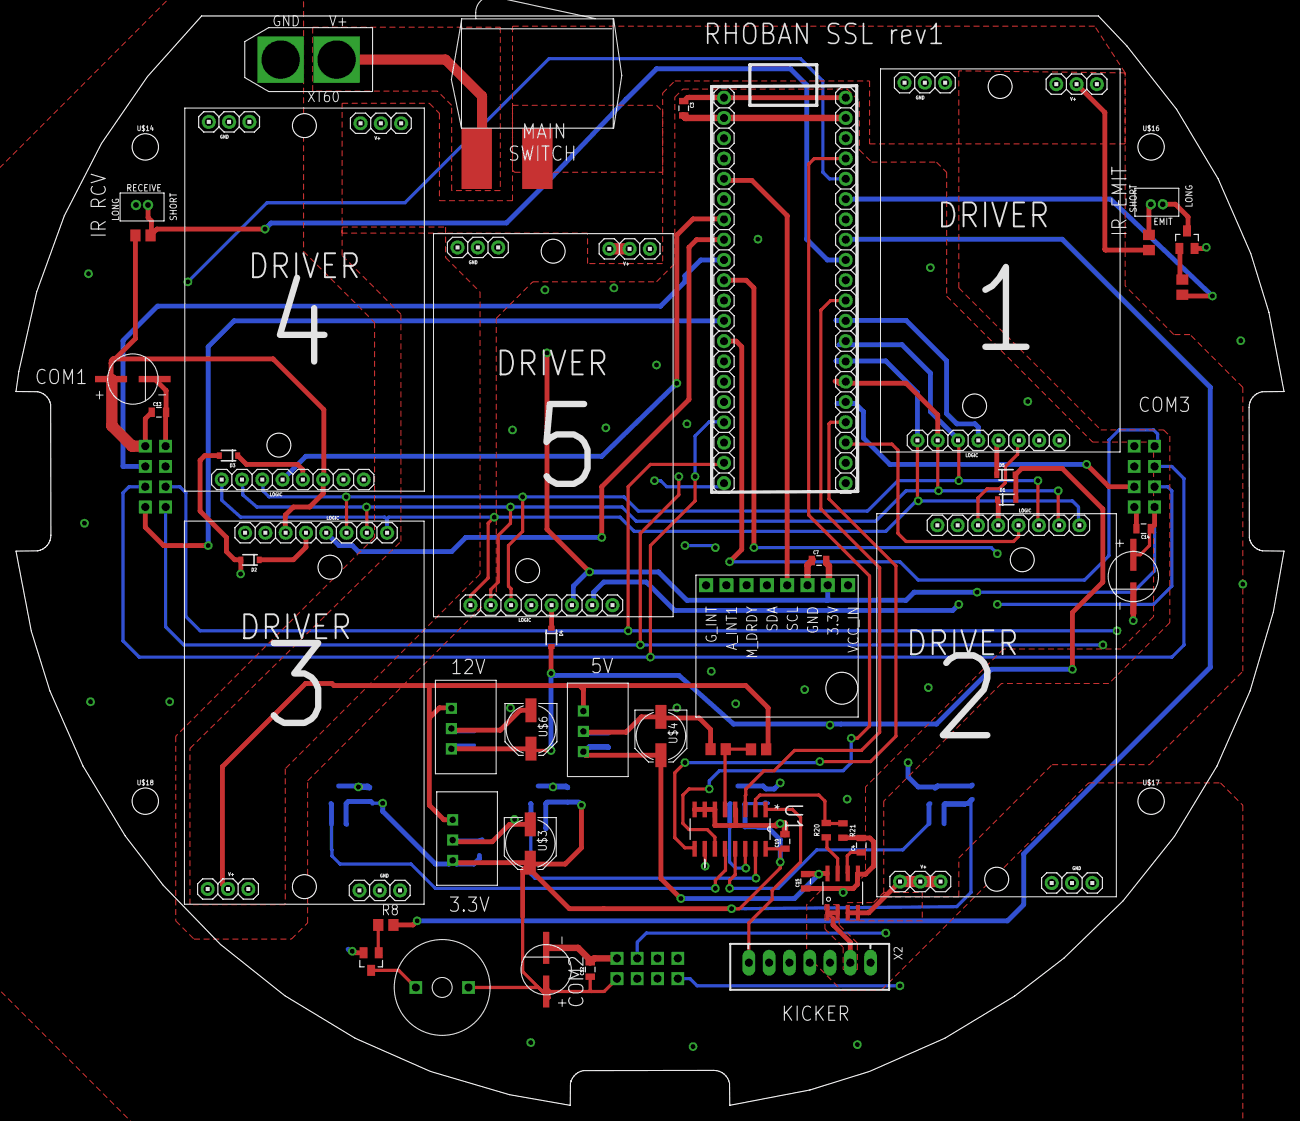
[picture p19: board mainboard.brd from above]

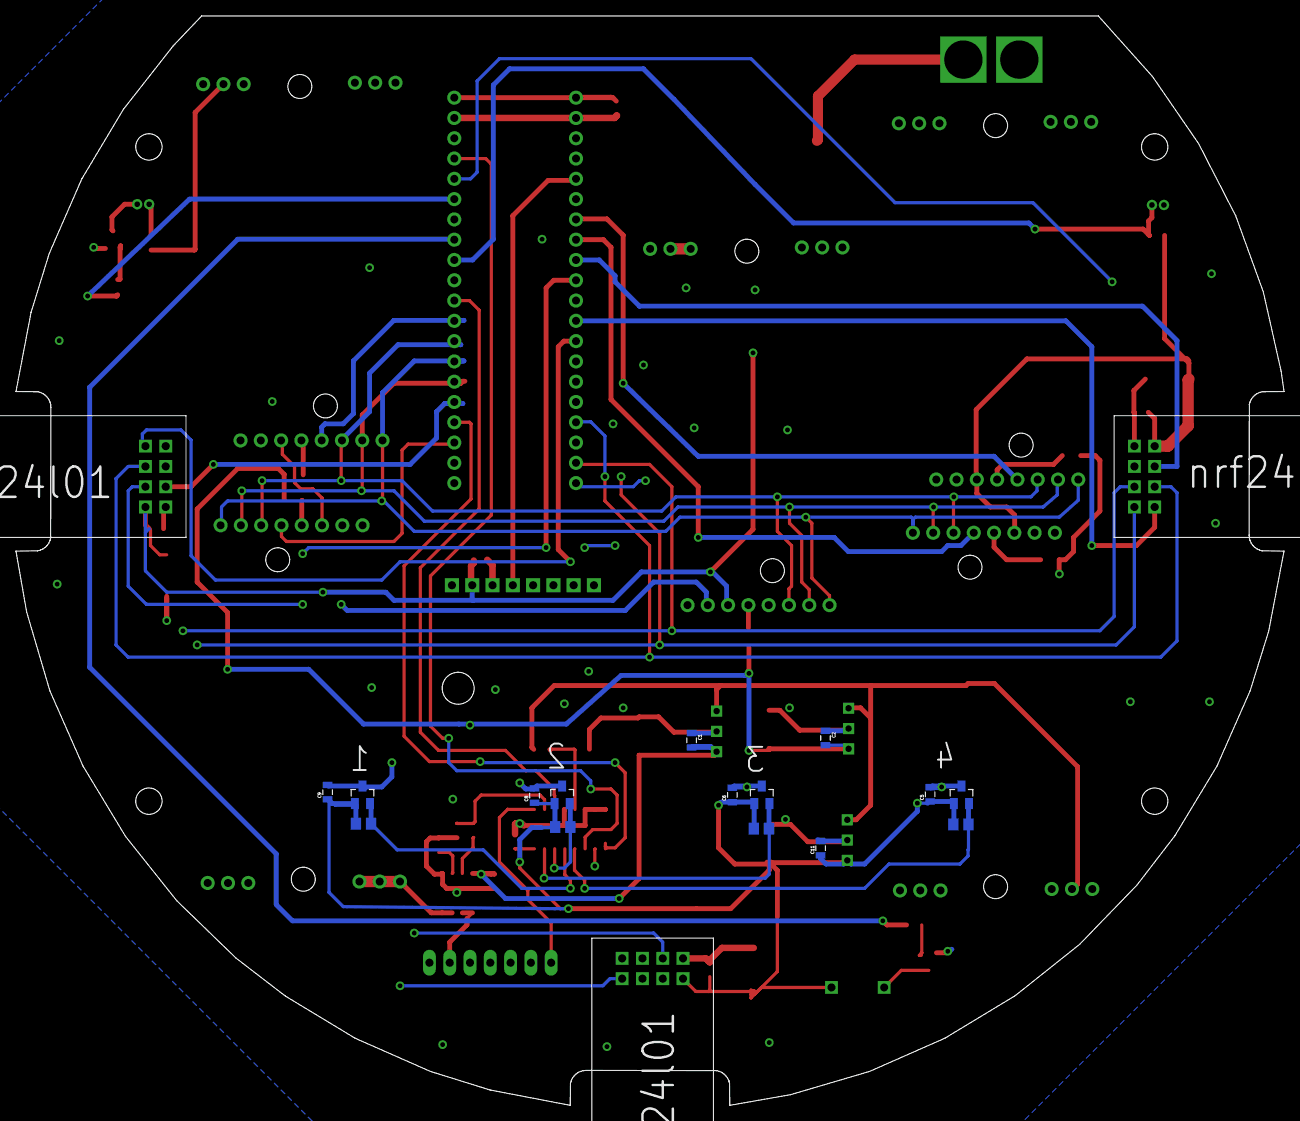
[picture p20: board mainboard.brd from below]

Board: 4 copper layers, 158.8 x 136.4 mm, 69 parts (18 on the bottom side), 58 nets.

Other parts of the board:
U$14, U$16, U$17, U$18: STAND-OFF

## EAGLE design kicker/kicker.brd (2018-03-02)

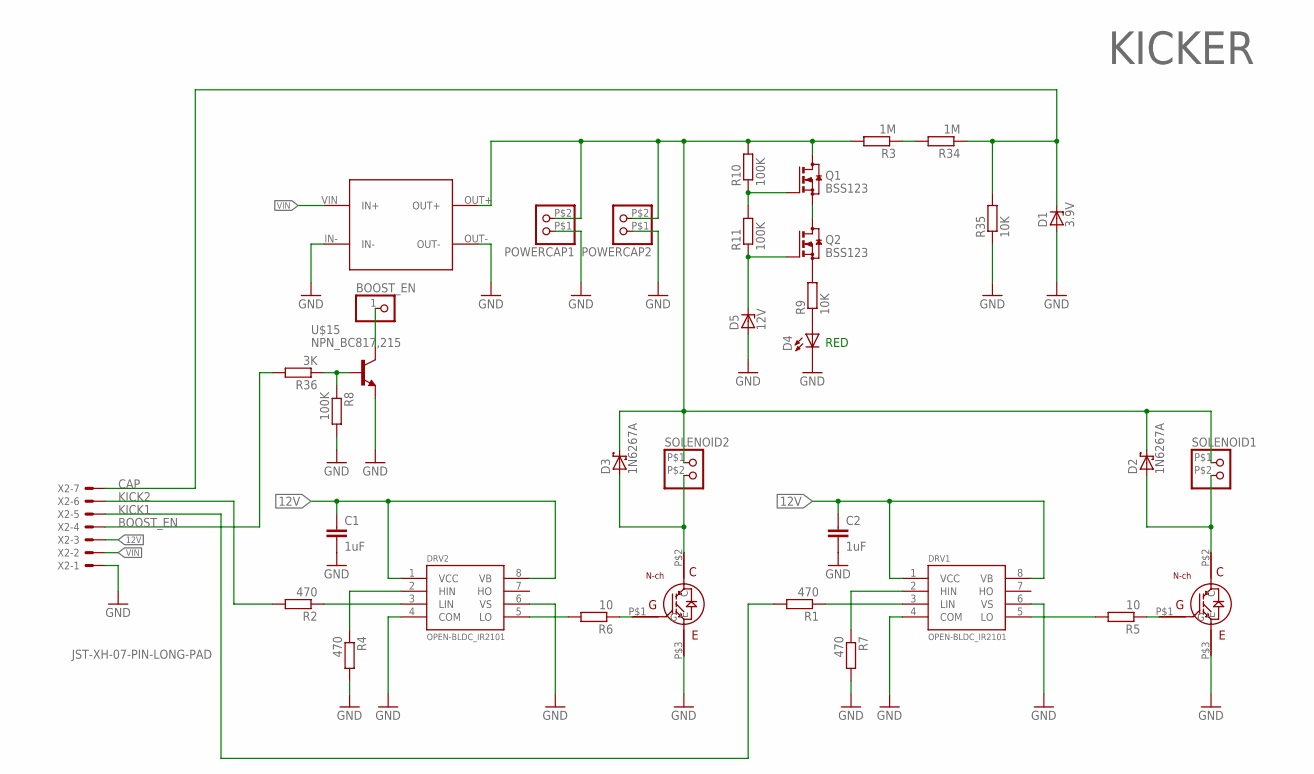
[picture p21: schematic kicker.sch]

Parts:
BOOST_EN: CONNEC_1X01
C1, C2: 1uF; C0805
D1: 3.9V; SOD80C; FARNELL 1097198
D2, D3: 1N6267A; C4111-15; FARNELL 9551735
D4: RED; LED-1206; FARNELL 1581233
D5: 12V; SOD80C; FARNELL 2319144
DRV1, DRV2: OPEN-BLDC_IR2101; OPEN-BLDC_SO-8; FARNELL 8638730
POWERCAP1, POWERCAP2: CONNEC_1X02BIG; CONNEC_1X02_BIG
Q1, Q2: BSS123; SOT23
R1, R2, R4, R7: 470; R0805; FARNELL 2446965
R3, R34: 1M; R0805; FARNELL 2129375
R5, R6: 10; R0805; FARNELL 2446965
R8: 100K; R0805; FARNELL 2446965
R9, R35: 10K; R0805; FARNELL 2447553
R10, R11: 100K; R0805; FARNELL 2447553
R36: 3K; R0805; FARNELL 2446965
SOLENOID1, SOLENOID2: CONNEC_1X02BIG; CONNEC_1X02_BIG
U$1, U$11: TO-247A; TO-247; FARNELL 2429705
U$5: BOOSTER; BOOSTER_390V
U$15: NPN_BC817,215; SOT-23; FARNELL 1081223
X2: JST-XH-07-PIN-LONG-PAD; JST-XH-07-PACKAGE-LONG-PAD

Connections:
12V: C1.1, C2.1, DRV1.1 (VCC), DRV1.8 (VB), DRV2.1 (VCC), DRV2.8 (VB), X2.3
BOOST_EN: R36.2, X2.4
CAP: D1.C, R34.1, R35.2, X2.7
GND: C1.2, C2.2, D1.A, D4.C, D5.A, DRV1.4 (COM), DRV1.6 (VS), DRV2.4 (COM), DRV2.6 (VS), POWERCAP1.P$1 (1), POWERCAP2.P$1 (1), R4.2, R7.2, R8.2, R35.1, U$1.P$3 (E), U$5.IN-, U$5.OUT-, U$11.P$3 (E), U$15.2 (E), X2.1
KICK1: R1.2, X2.5
KICK2: R2.2, X2.6
unnamed: DRV2.3 (LIN), R2.1
unnamed: D2.A, SOLENOID1.P$2 (2), U$1.P$2 (C)
unnamed: DRV2.5 (LO), R6.2
unnamed: R3.1, R34.2
unnamed: DRV1.3 (LIN), R1.1
unnamed: DRV2.2 (HIN), R4.1
unnamed: R5.1, U$1.P$1 (G)
unnamed: R6.1, U$11.P$1 (G)
unnamed: DRV1.5 (LO), R5.2
unnamed: Q2.2 (S), R9.2
unnamed: D4.A, R9.1
unnamed: Q1.2 (S), Q2.3 (D)
unnamed: DRV1.2 (HIN), R7.1
unnamed: Q1.1 (G), R10.1, R11.2
unnamed: D5.C, Q2.1 (G), R11.1
unnamed: D3.A, SOLENOID2.P$2 (2), U$11.P$2 (C)
unnamed: BOOST_EN.1, U$15.3 (C)
unnamed: R8.1, R36.1, U$15.1 (B)
VBOOST: D2.C, D3.C, POWERCAP1.P$2 (2), POWERCAP2.P$2 (2), Q1.3 (D), R3.2, R10.2, SOLENOID1.P$1 (1), SOLENOID2.P$1 (1), U$5.OUT+
VIN: U$5.VIN (IN+), X2.2

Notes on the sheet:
KICKER
RED

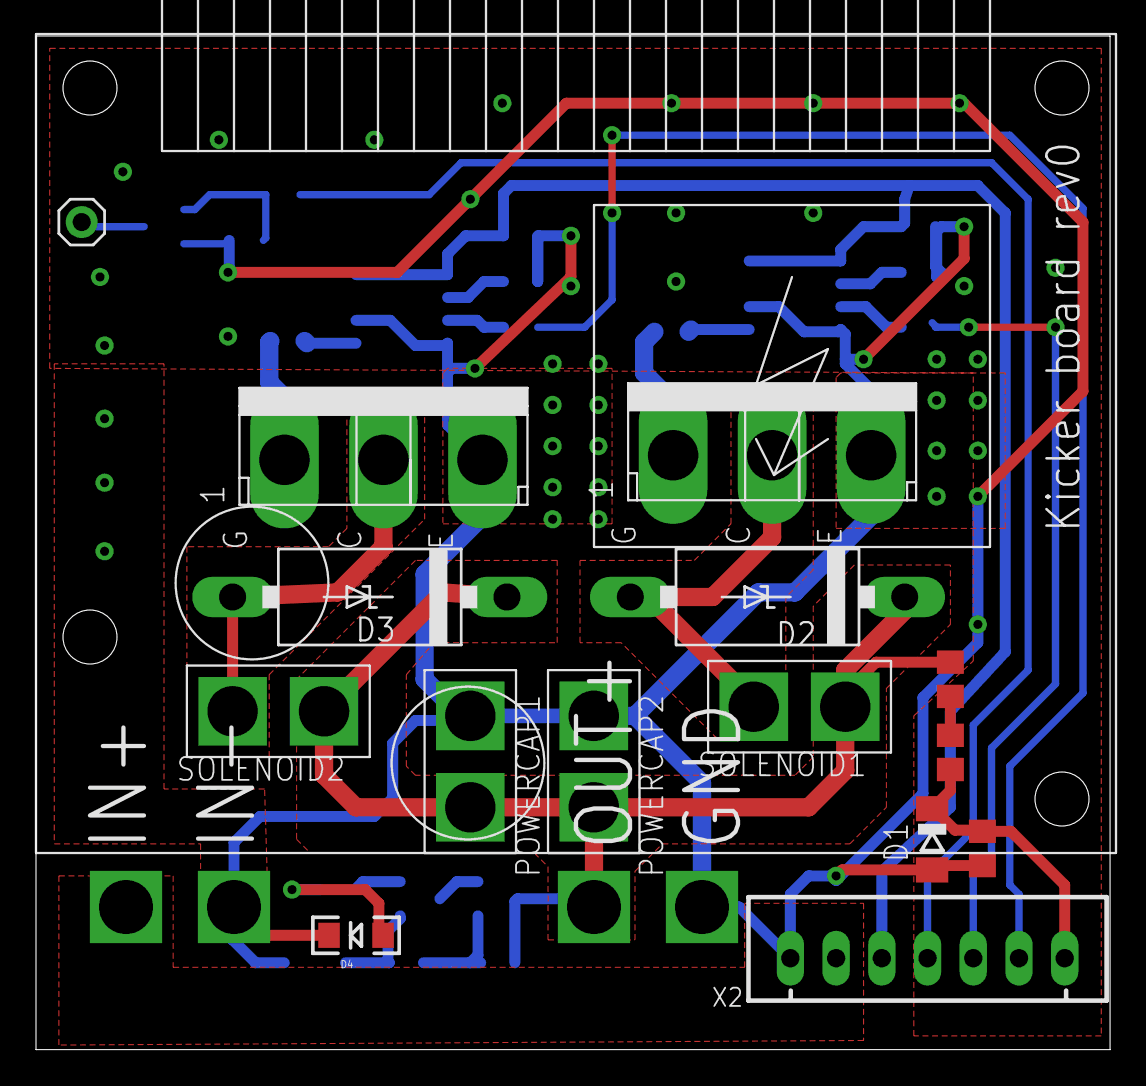
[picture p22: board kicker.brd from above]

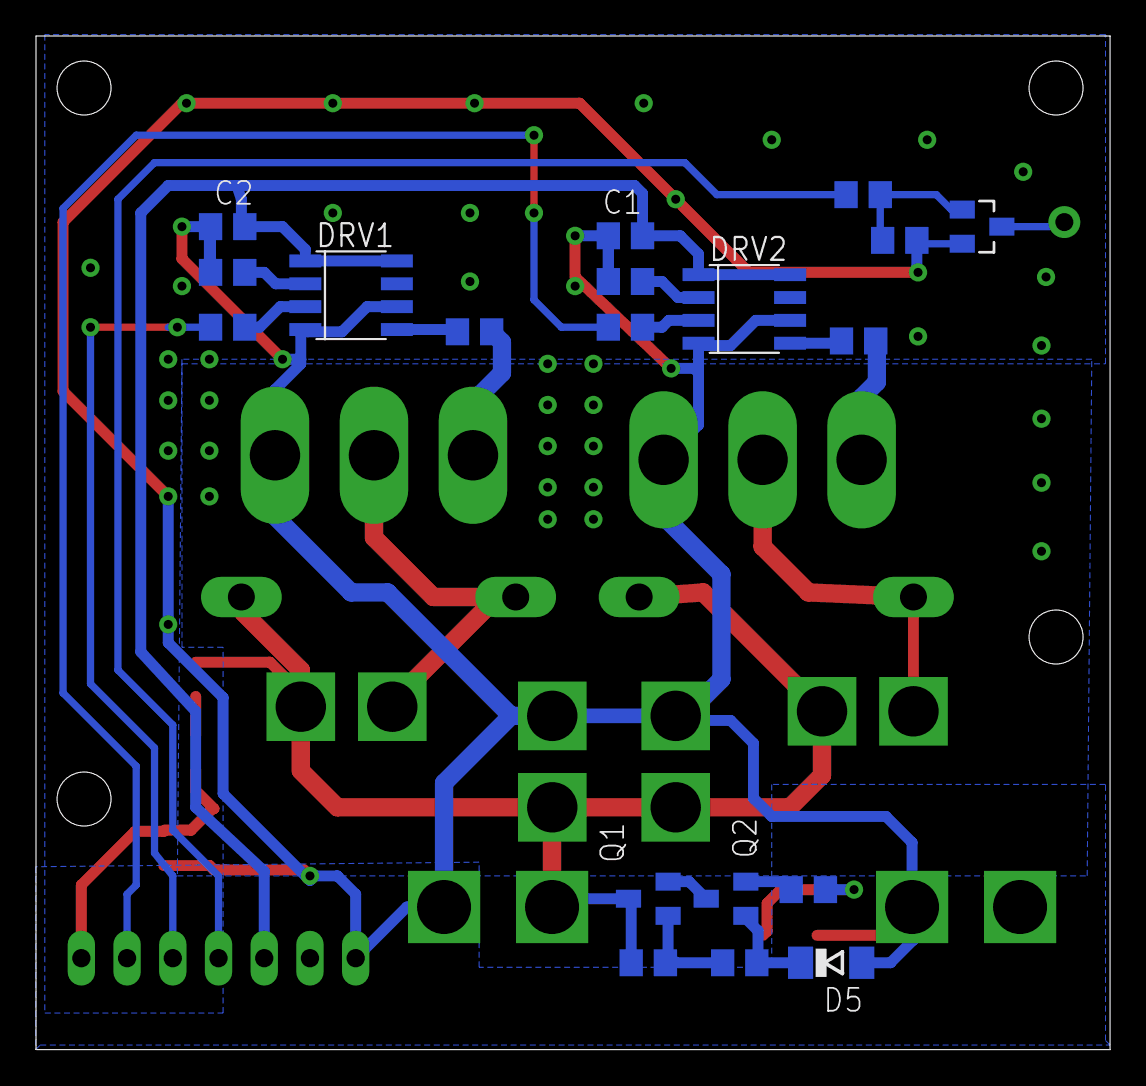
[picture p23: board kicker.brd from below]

Board: 2 copper layers, 59.7 x 56.3 mm, 35 parts (19 on the bottom side), 26 nets.

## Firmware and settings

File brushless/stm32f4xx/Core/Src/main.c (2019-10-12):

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

/* Includes ------------------------------------------------------------------*/
#include "main.h"
#include "usb_device.h"

/* USER CODE BEGIN Includes */
#include <terminal.h>
#include "debug.h"
#include "usbd_cdc_if.h"
#include <time.h>
#include <encoder.h>
#include <system.h>
#include <motor.h>
#include <foc.h>
#include <errors.h>
#include <observer.h>
#include <priority.h>
#include <frequence_definitions.h>
#include <current.h>
#include <pwm.h>

// TIM1 is a center-aligned timer
#define TIM1_PERIOD CA_RELOAD(2*PWM_PERIOD) // The timer to generate all the pwm

// TIM2 is a counter-up timer
#define TIM2_PERIOD CU_RELOAD(PWM_PERIOD) // The timer to generate all the pwm
//#define TIM2_CC2_PULSE (PWM_PERIOD-CURRENT_MEDURE_HALF_PERIOD)
#define TIM2_CC2_PULSE delay_period
_Static_assert(TIM2_CC2_PULSE>0, "");
_Static_assert(TIM2_CC2_PULSE<PWM_PERIOD, "");
#define TIM2_CC1_PULSE TIM2_CC2_PULSE

// TIM3 is a counter-up timer
#define TIM3_PERIOD CU_RELOAD(SYCLK_TO_ENCODER_PERIOD) // Timer for the encoder.
#define TIM4_PERIOD 4 // Clock user to reset and synchronize all the other clock
#define TIM5_PERIOD 4294967295 // Clock used to launch background computation
#define TIM1_PRESCALAR 0
#define TIM3_PRESCALAR 0
#define TIM4_PRESCALAR 0
#define TIM5_PRESCALAR 1 //5000
#define COMP_DELAY 1
/* USER CODE END Includes */

ADC_HandleTypeDef hadc1;
DMA_HandleTypeDef hdma_adc1;

SPI_HandleTypeDef hspi2;
DMA_HandleTypeDef hdma_spi2_rx;
DMA_HandleTypeDef hdma_spi2_tx;

TIM_HandleTypeDef htim1;
TIM_HandleTypeDef htim2;
TIM_HandleTypeDef htim3;
TIM_HandleTypeDef htim4;
TIM_HandleTypeDef htim5;

/* USER CODE BEGIN PV */
__IO uint16_t adc_data[ADC_DATA_SIZE] = {0};
extern volatile bool start_adc;
/* USER CODE END PV */

void SystemClock_Config(void);
static void MX_GPIO_Init(void);
static void MX_DMA_Init(void);
static void MX_SPI2_Init(void);
static void MX_TIM1_Init(void);
static void MX_TIM2_Init(void);
static void MX_TIM3_Init(void);
static void MX_TIM4_Init(void);
static void MX_TIM5_Init(void);
static void MX_ADC1_Init(void);
/* USER CODE BEGIN 0 */
TERMINAL_COMMAND(frequences, "Print all the frequences"){

  terminal_println( "Frequences :");
  terminal_println("");
  terminal_print("CLK_SYSCLK :");
  terminal_println_int(CLK_SYSCLK);
  terminal_print("PWM_FREQ :");
  terminal_println_int(PWM_FREQ);
  terminal_print("CENTER_ALIGNED_PWM_FREQ :");
  terminal_println_int(CENTER_ALIGNED_PWM_FREQ);
  terminal_print("ENCODER_FREQ :");
  terminal_println_int(ENCODER_FREQ);
  //terminal_print("ANGLE_OBSERVER_FREQ :");
  //terminal_println_int(ANGLE_OBSERVER_FREQ);
  terminal_print("PWM_DUTY_CYCLE_FREQ :");
  terminal_println_int(PWM_DUTY_CYCLE_FREQ);
  //terminal_print("ARG_COMMAND_FREQ :");
  //terminal_println_int(ARG_COMMAND_FREQ);
  //terminal_print("ANGLE_FREQ :");
  //terminal_println_int(ANGLE_FREQ);
  terminal_print("NORM_COMMAND_FREQ :");
  terminal_println_int(NORM_COMMAND_FREQ);
  terminal_print("AS5047D_UPDATE_FREQ : ");
  terminal_println_int(AS5047D_UPDATE_FREQ);
  terminal_print("AS5047D_UPDATE_FAILURE_FREQ : ");
  terminal_println_int(AS5047D_UPDATE_FAILURE_FREQ);

  terminal_println("");
  terminal_println("Periods :");
  terminal_println("");
  terminal_print("PWM_PERIOD :");
  terminal_println_int(PWM_PERIOD );
  terminal_print("CENTER_ALIGNED_PERIOD :");
  terminal_println_int(CENTER_ALIGNED_PERIOD);
  terminal_print("ENCODER_PERIOD :");
  terminal_println_int(ENCODER_PERIOD);
  //terminal_print("OBS_PERIOD :");
  //terminal_println_int(OBS_PERIOD);
  terminal_print("PWM_DUTY_CYCLE_PERIOD :");
  terminal_println_int(PWM_DUTY_CYCLE_PERIOD);
  terminal_print("NORM_PERIOD :");
  terminal_println_int(NORM_PERIOD);
  terminal_print("TIM1_PERIOD :");
  terminal_println_int(TIM1_PERIOD);
  terminal_print("TIM3_PERIOD :");
  terminal_println_int(TIM3_PERIOD);
  terminal_print("TIM4_PERIOD :");
  terminal_println_int(TIM4_PERIOD);
  terminal_print("TIM5_PERIOD :");
  terminal_println_int(TIM5_PERIOD);
  terminal_print("AS5047D_TIME_ns : ");
  terminal_println_int(AS5047D_TIME_ns);
  terminal_print("AS5047D_TIME_FAILURE_ns : ");
  terminal_println_int(AS5047D_TIME_FAILURE_ns);

  terminal_println("");
  terminal_println("Max values :");
  terminal_println("");
  terminal_print("MAXIMAL_PHASE_MOTOR_FREQ :");
  terminal_println_int(MAXIMAL_PHASE_MOTOR_FREQ);
  terminal_print("MAXIMAL_MOTOR_VELOCITY :");
  terminal_println_int(MAXIMAL_MOTOR_VELOCITY);

  terminal_println("");
  terminal_println("sampling factors :");
  terminal_println("");
  terminal_print("OVERSAMPLING_NUMBER :");
  terminal_println_int(OVERSAMPLING_NUMBER);
  terminal_print("NYQUIST_FACTOR :");
  terminal_println_int(NYQUIST_FACTOR);

  terminal_println("");
  terminal_println("Pulse :");
  terminal_print("ENC_SPI_DELAY :");
  terminal_println_int(ENC_SPI_DELAY);
}

TERMINAL_COMMAND(version, "firmware version")
{
  terminal_println(FIRMWARE_VERSION);
}

TERMINAL_COMMAND(led, "Set led")
{
  if(argc == 0){
    LED;
  }else if(argc == 1){
    if( atoi(argv[0])==1 ){
      LED_ON;
    }else{
      LED_OFF;
    }
  }else{
    terminal_println("Usage: led [1|0]");
  }
}

TERMINAL_COMMAND(test_us, "test micro oscillation on LED.")
{
  while(1){
    delay_us(1);
    LED;
  }
}

#ifdef DEBUG
TERMINAL_COMMAND(test_ms, "test milli oscillation on LED.")
{
  while(1){
    DELAY_MS(1);
    LED;
  }
}
#endif

TERMINAL_COMMAND(test_ns, "test milli oscillation on LED.")
{
  while(1){
    DELAY_AT_LEAST_NS(350);
    LED;
  }
}

void HAL_ADC_ErrorCallback(ADC_HandleTypeDef *hadc){
  if(hadc == &hadc1){
    RAISE_ERROR;
  }
}

void HAL_SPI_ErrorCallback(SPI_HandleTypeDef* hspi){
  if(hspi == &hspi2){
    encoder_error_spi_call_back();
  }
}

void HAL_SPI_TxRxCpltCallback(SPI_HandleTypeDef* hspi){
  if(hspi == &hspi2){
    encoder_spi_call_back();
  }
}

TERMINAL_PARAMETER_BOOL(st, "decl", false);

void start_and_synchronize_timers(){
  // We start timer 1, 2 and 4
  if( HAL_TIM_Base_Start(&htim1) != HAL_OK ){
    raise_error(ERROR_TIMER_INIT_AT_LINE, __LINE__);
  }
  if( HAL_TIM_Base_Start(&htim2) != HAL_OK ){
    raise_error(ERROR_TIMER_INIT_AT_LINE, __LINE__);
  }
  if( HAL_TIM_Base_Start(&htim3) != HAL_OK ){
    raise_error(ERROR_TIMER_INIT_AT_LINE, __LINE__);
  }
  
  //
  // Now, we will synchronize all timer by using the timer 4
  // Timer 4 is configured to send a trigger output (whose name is ITR3)
  // at each update.
  // Timer 1, 2, 3 are in slave mode, configured in reset mode and are waiting
  // for an input signal from TIM 4 (by using ITR3) to be reseted.
  //  
  if( HAL_TIM_Base_Start(&htim4) != HAL_OK ){
     raise_error(ERROR_TIMER_INIT_AT_LINE, __LINE__);
  }
  delay_us(1); // We wait a little, to give time to TIM4 to be updated() (and 
  //DELAY_MS(10000); // We wait a little, to give time to TIM4 to be updated() (and 
                // ant trigger an output signal.
  if( HAL_TIM_Base_Stop(&htim4) != HAL_OK ){
    raise_error(ERROR_TIMER_INIT_AT_LINE, __LINE__);
  }

  // We can now start the PWM of timer 2
  #ifdef PWM_ON_FOR_ADC_TICK
    if( HAL_TIM_PWM_Start(&htim2, TIM_CHANNEL_1) != HAL_OK ){
      RAISE_ERROR;
    }
  #endif
  if( HAL_TIM_PWM_Start(&htim2, TIM_CHANNEL_2) != HAL_OK ){
    raise_error(ERROR_CURRENT, ADC_PWM);
  }
  #ifdef PWM_ON_FOR_ENCODER_TICK
    if( HAL_TIM_PWM_Start(&htim3, TIM_CHANNEL_2) != HAL_OK ){
      RAISE_ERROR;
    }
  #endif
  // We can now start Output compare for 2 
  //if( HAL_TIM_OC_Start(&htim2, TIM_CHANNEL_2) != HAL_OK){
  //  raise_error(ERROR_TIMER_INIT_AT_LINE, __LINE__);
  //};

  // We can now start Output compare and interuption for timer 1, 2 and 3.
  if( HAL_TIM_OC_Start(&htim3, TIM_CHANNEL_1) != HAL_OK){
    raise_error(ERROR_TIMER_INIT_AT_LINE, __LINE__);
  };
  if( HAL_TIM_OC_Start_IT(&htim3, TIM_CHANNEL_1) != HAL_OK){
    raise_error(ERROR_TIMER_INIT_AT_LINE, __LINE__);
  };

  if( HAL_TIM_Base_Start_IT(&htim3) != HAL_OK ){
    raise_error(ERROR_TIMER_INIT_AT_LINE, __LINE__);
  }

  if( HAL_TIM_Base_Start(&htim5) != HAL_OK ){
    raise_error(ERROR_TIMER_INIT_AT_LINE, __LINE__);
  }
  if( HAL_TIM_OC_Start(&htim5, TIM_CHANNEL_1) != HAL_OK){
    raise_error(ERROR_TIMER_INIT_AT_LINE, __LINE__);
  };
  if( HAL_TIM_OC_Start_IT(&htim5, TIM_CHANNEL_1) != HAL_OK){
    raise_error(ERROR_TIMER_INIT_AT_LINE, __LINE__);
  };
}

volatile bool complete_current_adc = false;
// Call back when ADC is finishedDC
void HAL_ADC_ConvCpltCallback(ADC_HandleTypeDef* hadc){
//void HAL_ADC_ConvHalfCpltCallback(ADC_HandleTypeDef* hadc){
  if( hadc == &hadc1 ){
    //COOLDOWN(1000000){
    //  uint32_t v = hadc1.Instance->SR;
    //  BINT(v);
    //}
    #if 0
    COOLDOWN(2000000){
      terminal_println("-");
      for( uint32_t i=0; i< ADC_DATA_SIZE; i++ ){
        terminal_print("ADC : ");
        terminal_println_float(
          ((adc_data[i]-2048.0)*STM32_ADC_VOLTAGE_MAX*CURRENT_AO_GAIN)/4096
        );
      }
    }
    #endif
    complete_current_adc = true;
  }
}
/* USER CODE END 0 */


static volatile uint32_t sr, cr1, cr2; 
/**
  * @brief  The application entry point.
  * @retval int
  */
int main(void)
{
  

  /* MCU Configuration--------------------------------------------------------*/

  /* Reset of all peripherals, Initializes the Flash interface and the Systick. */
  HAL_Init();

  /* Configure the system clock */
  SystemClock_Config();

  /* Initialize all configured peripherals */
  MX_GPIO_Init();
  MX_DMA_Init();
  MX_SPI2_Init();
  MX_TIM1_Init();
  MX_TIM2_Init();
  MX_TIM3_Init();
  MX_TIM4_Init();
  MX_TIM5_Init();
  MX_USB_DEVICE_Init();
  MX_ADC1_Init();
  /* USER CODE BEGIN 2 */


  serial_init();
  terminal_init(get_serial());
  
  system_init();
  #if defined(USE_INTERNAL_ENCODER)
    // We disactivate the External encoder
    HAL_GPIO_WritePin(ENC_EXT_CS_GPIO_Port, ENC_EXT_CS_Pin, GPIO_PIN_SET);
    encoder_init(&hspi2, ENC_INT_CS_GPIO_Port,ENC_INT_CS_Pin);
    #if defined(USE_EXTERNAL_ENCODER)
    _Static_assert(false, "EXTERNAL AND INTERNAL ENCODER IS NOT SUPPORTED.");
    #endif
  #elif defined(USE_EXTERNAL_ENCODER)
    // We disactivate the Internal encoder
    HAL_GPIO_WritePin(ENC_INT_CS_GPIO_Port, ENC_INT_CS_Pin, GPIO_PIN_SET);
    encoder_init(&hspi2, ENC_EXT_CS_GPIO_Port,ENC_EXT_CS_Pin);
  #else
    _Static_assert(false,"An encoder should be defined.");
  #endif
  observer_init();
  motor_init();
  foc_init();
  #ifdef ACTIVATE_LOG
  log_init();
  #endif

  start_and_synchronize_timers();

  start_adc = true;
 
  sr = hadc1.Instance->SR;
  cr1 = hadc1.Instance->CR1;
  cr2 = hadc1.Instance->CR2;
  encoder_start();
  motor_start();
  /* USER CODE END 2 */

  /* Infinite loop */
  /* USER CODE BEGIN WHILE */
  while (1)
  {


    system_tick();
    encoder_tick();
    serial_tick();
    terminal_tick();
    #ifdef ACTIVATE_LOG
    log_tick();
    #endif
    /* USER CODE END WHILE */

    /* USER CODE BEGIN 3 */
  }
  /* USER CODE END 3 */
}

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


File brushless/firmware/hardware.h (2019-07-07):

#ifndef _HARDWARE_H
#define _HARDWARE_H

#include "ssl.h"

// Flash address to write/read infos
#define INFO_FLASH_ADDR    0x0801FC00


// Defines the driver type (see below)
#define DRIVER_TYPE     TYPE_70W

#define TYPE_30W        1
#define TYPE_70W        2
#define TYPE_DRIBBLER   3

#ifndef DRIVER_TYPE
#error "You should set a value for DRIVER_TYPE"
#endif

// Encoder configuration
#if DRIVER_TYPE == TYPE_30W
#define ENCODER_QUADRATURE          // Quadrature encoder A/B
#define ENCODER_CPR      1024
#endif

#if DRIVER_TYPE == TYPE_70W
#define ENCODER_MAGNETIC            // Magnetic AS5048 14bit encoder
// #define ENCODER_CPR      1024
#define ENCODER_CPR      16384
// #define ENCODER_NONE                // No encoder
#endif

#if DRIVER_TYPE == TYPE_DRIBBLER
#define ENCODER_NONE                // No encoder
#endif

#define GREG 1
#define CATIE 2

#ifdef CATIE_BOARD
  #define BOARD CATIE
#endif
#ifdef GREG_BOARD
  #define BOARD GREG
#endif
#ifndef BOARD
  static_assert(false);
#endif

#if BOARD == CATIE
  #define REVERSE_HALL_PHASE
  // For SPI based encoders
  #define ENCODER_SPI         2
  #define ENCODER_SELECT_PIN  PB12
  #define ENCODER_SELECT_PIN_2  PC9
  #define ENCODER_INDEX_PIN   12 // Used to make a shift bit to define PB12

  // Current sensing
  #define CURRENT_U_PIN      PC0
  #define CURRENT_V_PIN      PC3
  #define CURRENT_W_PIN      PC1
  #define CURRENT_REF_PIN      PC2

  // Motors pins

  #ifdef REVERSE_PHASE
      #define U_SD_PIN       PC6  //use Timer 1 (Maple)
      #define U_IN_PIN       PA8  //use Timer 1 (Maple)

      #define V_SD_PIN       PC8  //use Timer 1 (Maple)
      #define V_IN_PIN       PA10  //use Timer 1 (Maple)

#define W_SD_PIN       PC7 //use Timer 1 (Maple)
#define W_IN_PIN       PA9 //use Timer 1 (Maple)
  #else
      #define U_SD_PIN       PC6 //use Timer 1 (Maple)
      #define U_IN_PIN       PA8 //use Timer 1 (Maple)

      #define V_SD_PIN       PC7 //use Timer 1 (Maple)
      #define V_IN_PIN       PA9 //use Timer 1 (Maple)

      #define W_SD_PIN       PC8  //use Timer 1 (Maple)
      #define W_IN_PIN       PA10 //use Timer 1 (Maple)
  #endif



  #ifdef REVERSE_HALL_PHASE
    #define HALLU_PIN        PA0
    #define HALLW_PIN        PA1
    #define HALLV_PIN        PA2
  #else
    #define HALLU_PIN        PA0
    #define HALLV_PIN        PA1
    #define HALLW_PIN        PA2
  #endif

  // SPI slave pin
  #define SLAVE_SPI           1
  #define SLAVE_PIN PA4
  #define SLAVE_CLK_PIN PA5
  #define SLAVE_MISO_PIN PA6
  #define SLAVE_MOSI_PIN PA7

  // Board LED pin
  #define LED_PIN     PB1
#endif

#if BOARD == GREG
  // For SPI based encoders
  #define ENCODER_SPI         2
  #define ENCODER_SELECT_PIN  31
  #define ENCODER_INDEX_PIN   12

  // Current sensing
  #define CURRENT_PIN      4

  // Motors pins

  #ifdef REVERSE_PHASE
      #define U_SD_PIN        10  //use Timer 2 (Maple Mini)
      #define U_IN_PIN       11  //use Timer 2 (Maple Mini)

      #define V_SD_PIN        33  //use Timer 3 (Maple Mini)
      #define V_IN_PIN       3  //use Timer 2 (Maple Mini)

#define W_SD_PIN        8 //use Timer 2 (Maple Mini)
#define W_IN_PIN       9 //use Timer 2 (Maple Mini)
  #else
      #define U_SD_PIN        10 //use Timer 2 (Maple Mini)
      #define U_IN_PIN       11 //use Timer 2 (Maple Mini)

      #define V_SD_PIN        8 //use Timer 2 (Maple Mini)
      #define V_IN_PIN       9 //use Timer 2 (Maple Mini)

      #define W_SD_PIN        33  //use Timer 3 (Maple Mini)
      #define W_IN_PIN       3 //use Timer 2 (Maple Mini)
  #endif


  #ifdef REVERSE_HALL_PHASE
    #define HALLU_PIN        7
    #define HALLW_PIN        6
    #define HALLV_PIN        5
  #else
    #define HALLU_PIN        7
    #define HALLV_PIN        6
    #define HALLW_PIN        5
  #endif

  // SPI slave pin
  #define SLAVE_SPI           1
  #define SLAVE_PIN           20

  // Board LED pin
  #define LED_PIN     22
  //#define LED_PIN     PB1
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

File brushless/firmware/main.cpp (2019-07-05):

#include <stdlib.h>
#include <wirish/wirish.h>
#include <libmaple/iwdg.h>
#include <terminal.h>
#include <main.h>
#include <series/gpio.h>
#include <watchdog.h>
#include "encoder.h"
#include "current.h"
#include "motor.h"
#include "com.h"
#include "servo.h"
#include "hardware.h"
#include "info.h"
#include <flash_write.h>
#include "motor_foc.h"

#define TEST_LED

//ONLY ONCE WHEN CONFIGURING THE MOTOR
#define SHOULD_DO_THE_TARE
//////


static bool is_tared=false;
static struct motor_info info;
/**
 * Setup function
 */
void setup()
{
  // init();
  // info_init();


#ifndef SHOULD_DO_THE_TARE
  //Read the f*cking flash
  flash_read(INFO_FLASH_ADDR, (void *)&info, sizeof(motor_info));
  set_origin(info.tare_value);
#else
  //WE WRITE THE TARE INTO THE FLASH
  //1) Activate SHOULD_DO_THE_TARE
  //2) Start the motor and type the tare cmd in terminak
  //3) put the returned value below
  //4) compile/upload/restart
  //5) Comment the SHOULD_DO_THE_TARE
  //6) compile/upload/restart
  info.tare_value=42; //PUT HERE THE VALUE GIVEN BY THE TARE CMD
  info_set(info);
#endif



  // Initalizing communication
  com_init();

  // Initializng current  sensor
#ifndef CURRENT_DISABLE
  current_init();
#endif

  // Initalizing encoder
  encoder_init();

  // Initalizing motor
  motor_init();

  // Initializing servo
  servo_init();

  // Starting the watchdog
  watchdog_start(WATCHDOG_14MS);

  terminal_init(&SerialUSB);

#ifdef TEST_LED
  pinMode(LED_PIN, OUTPUT);
  digitalWrite(LED_PIN, LOW);
#endif

#ifdef SHOULD_DO_THE_TARE
  if(!is_tared){
    is_tared=true;
    launch_tare_motor();
  }
#endif
}


static int last_led = 0;

/**
 * Loop function
 */
void loop()
{
    // Feeding watchdog
    watchdog_feed();


    // Updating motor phases, this is also done in the hall pin interrupt but
    // it seems safe to do it often anyway
    motor_tick();

    // Updating current sensor value
    #ifndef CURRENT_DISABLE
    current_tick();
    #endif

    // Ticking the terminal
    terminal_tick();

    // Ticking encoder
    encoder_tick();

    // Ticking servo
    servo_tick();

    // Ticking com
    com_tick();
#ifdef TEST_LED
    int val = millis();
    static int cnt_led = 0;
    if( val - last_led > 100 and cnt_led < 4 ){
        cnt_led ++;
        //terminal_io()->println( "ok" );
        if( cnt_led % 2 ){
          digitalWrite(LED_PIN, HIGH);
        }else{
          digitalWrite(LED_PIN, LOW);
        }
        last_led = val;
    }
#endif


}

TERMINAL_COMMAND(term, "term test")
{
    terminal_io()->println("term works !");
}



TERMINAL_COMMAND(read_info, "Read motor info in flash")
{
  flash_read(INFO_FLASH_ADDR, (void *)&info, sizeof(motor_info));
  terminal_io()->print("Flash value: ");
  terminal_io()->println(info.tare_value);
}

TERMINAL_COMMAND(save_info, "Save info on flash")
{
  info_set(info);
  terminal_io()->println("Done");
}


TERMINAL_COMMAND(show_tare_flash, "Show read tare info")
{
  terminal_io()->print("Tare: ");
  terminal_io()->println(info.tare_value);

}

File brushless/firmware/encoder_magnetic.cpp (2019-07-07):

#include "hardware.h"
#ifdef ENCODER_MAGNETIC
#include <stdlib.h>
#include <wirish/wirish.h>
#include <terminal.h>
#include <watchdog.h>
#include "motor.h"
#include "encoder.h"
#include "servo.h"
#include "security.h"

HardwareSPI encoder(ENCODER_SPI);

// Counter value
static int32_t encoder_cnt = 0;
static uint16_t encoder_magnitude = 0;
static bool encoder_present = true;
static bool encoder_is_not_initialized = true;

inline bool parity_16_check( uint16_t x ){
    x ^= x >> 8;
    x ^= x >> 4;
    x ^= x >> 2;
    x ^= x >> 1;
    return (~x) & 1;
}



static int theta_out_0 = 0*THETA_OUT_SCALE;
static int theta_out_1 = 0*THETA_OUT_SCALE;
static int theta_out_2 = 0*THETA_OUT_SCALE;
static int theta_out_3 = 0*THETA_OUT_SCALE;
static int theta_out_4 = 0*THETA_OUT_SCALE;
static int theta_out_5 = 0*THETA_OUT_SCALE;
static int theta_out_6 = 0*THETA_OUT_SCALE;
static int theta_out_7 = 0*THETA_OUT_SCALE;
static int theta_out_8 = 0*THETA_OUT_SCALE;
static int encoder_speed = 0*ENCODER_SPEED_SCALE;
static int low_2_speed = 0*ENCODER_SPEED_SCALE;
static int low_3_speed = 0*ENCODER_SPEED_SCALE;
static int low_4_speed = 0*ENCODER_SPEED_SCALE;
static int low_8_speed = 0*ENCODER_SPEED_SCALE;

static int sum_speed = 0*ENCODER_SPEED_SCALE;
static int speed_0 = 0*ENCODER_SPEED_SCALE;
static int speed_1 = 0*ENCODER_SPEED_SCALE;
static int speed_2 = 0*ENCODER_SPEED_SCALE;
static int speed_3 = 0*ENCODER_SPEED_SCALE;
static int speed_4 = 0*ENCODER_SPEED_SCALE;
static int speed_5 = 0*ENCODER_SPEED_SCALE;
static int speed_6 = 0*ENCODER_SPEED_SCALE;
static int speed_7 = 0*ENCODER_SPEED_SCALE;


bool encoder_is_ok()
{
    return encoder_magnitude > 500;
}

bool encoder_is_present()
{
    return encoder_present;
}


static bool encoder_has_new_value = false;

static int encoder_read_state = -1;
static uint16_t encoder_read_result = 0;
static uint16_t encoder_read_magnitude = 0;

uint16_t magnetic_value = 0;
static int32_t encoder_deltas = 0;

inline int32_t encoder_compute_delta(uint16_t a, uint16_t b)
{
    int32_t delta = ((int32_t) b) - ((int32_t) a);

    if (delta > 0x1fff) {
        delta -= 0x4000;
    }
    if (delta < -0x1fff) {
        delta += 0x4000;
    }

    return delta;
}

static bool encoder_flag = false;


static float theta_3_d = 0.0;
static float theta_2_d = 0.0;
static float theta_1_d = 0.0;
static float theta_0_d = 0.0;

static float encoder_cnt_0_d = 0.0;
static float encoder_cnt_1_d = 0.0;
static float encoder_cnt_2_d = 0.0;
static float encoder_cnt_3_d = 0.0;

float num_d = 0.0;
float den_d = 0.0;

static bool is_writting = true;

static bool error_spi_comunication = false;
static bool error_flag = false;
static uint16_t error_register = 0;

static unsigned int error_flag_count = 0;
static unsigned int error_parity_count = 0;
static unsigned int error_value_count = 0;
static unsigned int error_spi_count = 0;

#define SCALE_TO_CLEAR_GPIO_PIN 16
#define SCALE_TO_SET_GPIO_PIN 0

extern "C"
{
void __irq_spi2()
{
    // We just have received 8 bits in the MISO pin.
    // We need to get the data and send other ones in the MOSI pin.
    if (spi_is_tx_empty(SPI2)) {
        switch (encoder_read_state) {
            case 0: {
                is_writting = true;
                // We get the first 8 bits of the magnetic datas send by the 
                // encoder in the MOSI interface.
                encoder_read_magnitude = (SPI2->regs->DR << 8);
                // We send the last 8 bits of the command to 
                // request an angle (0xffff).
                SPI2->regs->DR = 0xff;
                encoder_read_state++;
                break;
            }
            case 1: {
                // We get the last 8 bits of the magnetic datas send by the 
                // encoder in the MOSI interface?
                encoder_read_magnitude |= SPI2->regs->DR;
                #define DATA_MASK 0x3fff
                // We collect the magnitude data (the last 13 bits)
                encoder_magnitude = encoder_read_magnitude & DATA_MASK;
                
                // We start a new communication for a new request 
                GPIOB->regs->BSRR = (1U << ENCODER_INDEX_PIN) << SCALE_TO_SET_GPIO_PIN;
                delay_us(1);
                GPIOB->regs->BSRR = (1U << ENCODER_INDEX_PIN) << SCALE_TO_CLEAR_GPIO_PIN;
                delay_us(1);

                // We want to ask for and magnetic value. The command is 
                // 0x7ffe (P=0 to have a even number of bits, R=1 for a read 
                // command and Address=x3FFE to ask for an magnetic value).
                // we send the first 8bits of the command in the MOSI
                SPI2->regs->DR = 0x7f;
                encoder_read_state++;
                break;
            }
            case 2: {
                // We get the first 8 bits of the angle datas send by the 
                // encoder in the MOSI interface.
                encoder_read_result = (SPI2->regs->DR << 8);
                // We send the last 8 bits of the command to 
                // request a magnetic value (0x7ffe).
                SPI2->regs->DR = 0xfe;
                encoder_read_state++;
                break;
            }
            case 3: {
                // We get the last 8 bits of the angle datas send by the 
                // encoder in the MOSI interface.
                encoder_read_result |= SPI2->regs->DR;
                
                error_spi_comunication = false;
                error_flag = false;
                #if 1
                // We check no error occurs when we sent all
                // the previous commands (angle and magetic read commands)
                // to the encoder
                //if( encoder_read_result & 0x4000 ){
                //    error_flag_count++;
                //    security_set_warning(WARNING_ERROR_FLAG_ENCODER );
                //    error_spi_comunication = true;
                //    error_flag = true;
                //}
                #endif
                // We check the parity of the received datas for the
                // angle value. The magnetic value is not used.
                if(
                    ! parity_16_check(encoder_read_result & 0x7FFF) xor 
                    ( (encoder_read_result & 0x8000) !=0 )
                ){
                    error_parity_count++;
                    security_set_warning(WARNING_ERROR_PARITY_ENCODER);
                    error_spi_comunication = true;
                }
                if( error_spi_comunication ){
                      error_spi_count++;
                }

                // We collect the angle data (the last 13 bits)
                encoder_read_result &= DATA_MASK;
                is_writting = false;
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

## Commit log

2017-10-26 Moving to folders
    [brushless.brd, brushless.ods, brushless.sch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]
2017-12-21 Updating mainboard, using brushless drivers [wip]
    [mainboard.brd, mainboard.sch]
2017-12-27 Using 0.25 instead of 0.254 pad width for stm32
    [brushless.brd, brushless.sch]
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2018-01-09 fixes in com delay
    [com.cpp, drivers.cpp]
2018-01-10 kicker, voltage sampling & updating protocol
    [mainboard.brd]
2018-01-11 max pwm, max acc
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2018-01-16 Driver type system, adding dribbler
2018-01-16 not dribbling if servo_enable is false
2018-01-19 Fixing phase on bootstrap capcaitors
    [brushless.brd, brushless.sch]
2018-01-28 Changing ref for cap 100uF (fixes #18)
    [brushless.brd, brushless.sch]
2018-01-29 Separate kicker board
    [kicker.brd, kicker.sch]
2018-01-29 Mainboard rev1 wip
    [mainboard.brd, mainboard.sch]
2018-01-30 Updating designs
    [board.dxf, board.ipt, board.stl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]
2018-01-30 mainboard updates
    [mainboard.brd, mainboard.sch]
2018-01-30 Update mainboard
    [mainboard.brd, mainboard.sch]
2018-02-05 Adding resistor on big mos gates
    [kicker.brd, kicker.sch]
2018-02-05 farnell attrs
    [mainboard.brd, mainboard.sch]
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2018-02-08 VCC -> 5V in connectors.svg
2018-02-09 1K on grid
    [kicker.brd, kicker.sch]
2018-02-09 Minor placement changes
    [mainboard.brd]
2018-02-09 Farnel ATTRs
    [mainboard.brd, mainboard.sch]
2018-02-09 Updating BOMs and ATTRs
    [brushless.brd, brushless.sch, kicker.brd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]
2018-02-14 PWMizing only the high side of half bridges
2018-02-14 On-board kinematics, now the acceleration is limited by the robot and orders are x/y/t
2018-02-14 Adding optocoupler on the kick line
    [kicker.brd, kicker.sch]
2018-02-14 Moving to IR2103
    [brushless.brd, brushless.sch]
2018-02-14 Fix optocoupler
    [kicker.brd, kicker.sch]
2018-02-18 Adding multiplexer on mainboard, sampling charge current, separate com ces
    [mainboard.brd, mainboard.sch]
2018-02-18 Fixing mux addr, drivers #
    [mainboard.brd, mainboard.sch]
2018-02-19 Adding optional npn for kicking
    [kicker.brd, kicker.sch]
2018-02-19 Kicker rev0
    [kicker.brd, kicker.sch]
2018-02-19 rearranging rev0 board for 2 big moses
    [kicker.brd]
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2018-02-21 Always enabling pull up on hall sensors
2018-02-22 Using mos driver on kicker board
    [kicker.brd, kicker.sch, mainboard.brd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]
2018-02-22 no rev0 yet
    [kicker.brd, kicker.sch]
2018-02-22 10 ohms on mos gates
    [brushless.brd, brushless.sch]
2018-02-23 schematic modified on brushless board
    [brushless.brd, brushless.sch, mainboard.sch]
2018-02-25 brushless board rerouted
    [brushless.brd, brushless.sch]
2018-02-25 kicker board routed
    [kicker.brd, kicker.sch]
2018-02-25 unrouted net corrected
    [kicker.brd]
2018-02-25 clearence error on brushles board corrected
    [brushless.brd, brushless.sch]
2018-02-28 kicker rev0, brushless rev2
    [brushless.brd, brushless.sch, kicker.brd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]
2018-02-28 rev2 silk on bottom
    [brushless.brd]
2018-02-28 Master board is now dummy repeating the packets to the robots
2018-03-02 Passive values
    [kicker.brd, kicker.sch]
2018-03-02 Driver places
    [mainboard.brd]
2018-03-06 pwm lut is now in mainboard
2018-03-06 fixing which status is read
    [drivers.cpp]
2018-03-09 Bootstrap values
    [brushless.sch]
2018-03-19 Fixing rev2 board/sch consistency
    [brushless.brd]
2018-03-19 Improving values indications
    [brushless.brd, brushless.sch]
2018-03-26 Mainboard rev1
    [mainboard.brd, mainboard.sch]
2018-04-03 When pwm=0, enabling the low moses
2018-04-12 Passing drivers errors in status packet
    [com.cpp]
2018-04-12 Just looking for 4 drivers
2018-04-13 Voltage is now 8th of V
2018-04-20 Farnell BOM attributes
    [brushless.brd, brushless.sch]
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2018-05-11 Infos, triple antenna polling
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2018-05-22 Monitoring driver errors
2018-05-30 Revert "Servo update"
    This reverts commit 3e0cb52e1dc3d9a87e080885440580884add9c85.
    [motor.cpp, servo.cpp]
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2018-05-31 Stopping charge while kicking
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2018-06-12 Fixing encoder none
2018-06-12 Fixing no encoder mode
    [servo.cpp]
2018-06-13 Persisting kicker inverted wiring, increasing spin speed, changing IR rules
    [com.cpp, main.cpp]
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2018-07-18 Irq oriented handling of magnetic encoder
2019-02-15 Add velocity in encoder_magnetic
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2019-02-28 TBC. Saving : Remove motor TICK at HALL
2019-03-01 Remove some bug + add limits
    [motor.cpp, motor_foc.cpp, motor_foc.h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]
2019-03-02 Some improvement on REVERSE_PHASE
    [encoder_magnetic.cpp, hardware.h, motor_foc.cpp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]
2019-03-03 Now command vectorial compute correct pwm.
    [integer_calculus.py, motor_foc.cpp, motor_foc.py]
2019-03-04 Improve integer calculus in motor_foc
2019-03-14 First implementation of encoder filter
2019-03-15 Remove some errors and warnings
    [encoder_magnetic.cpp, motor_foc.cpp, ssl.h]
2019-03-25 Add packet reader for spi encoder
2019-03-30 Now motor pwm is set at 98khz
2019-04-01 Imrove frequence of motor command update
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2019-04-03 Solve problem of symetric calculus.
    [encoder_magnetic.cpp, integer_calculus.py, motor_foc.cpp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]
2019-04-12 Tools for testing current
2019-04-12 Solve some bug on sinus and cosinus
    [motor_foc.cpp, servo_hybrid.cpp, ssl.h]
2019-04-16 Remove bug on low state Hybrid
    [servo.cpp, servo_foc.cpp, servo_hybrid.cpp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]
2019-04-17 Remove bug on speed fir motor_foc
    [encoder.h, encoder_magnetic.cpp, motor_foc.cpp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]
2019-04-19 Fix defin ssl.h for real use
    [ssl.h]
2019-04-25 Change PIN definition + chesk USB + LED
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2019-04-26 Finish to port for the CATIE using stm32f103rb
2019-04-28 Add code to manage current
2019-06-01 Refactorise Hall and foc to have enable functions
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2019-06-02 Remove a bug in Hall
    [motor_hall.cpp, ssl.h]
2019-06-19 Improve SPI order in com
2019-06-23 Solve a bug ordinit in PIN initialization
    [motor_foc.cpp, motor_hall.cpp]
2019-06-23 Update hall for CATIE board
2019-06-26 Remove bug order on init
    [com.cpp, drivers.cpp, kicker.cpp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]
2019-06-27 Problem of kicker initialisation.
    [kicker.cpp]
2019-06-28 The Final release of Odometry exported from Odometry3 branch
2019-06-28 Revert a debugging #define
    [com.cpp]
2019-06-30 Remove a bug kicker
    [kicker.cpp]
2019-06-30 Add Led blinking in brushless + Reduce tare power
2019-07-01 fix hella shittons of bugs!
    [com.cpp, drivers.cpp, kicker.cpp]
2019-07-01 Maple bootloader for brushless board
    [flash.cfg, stm32.cfg]
2019-07-01 Solve a bug in mainboard initialisation
    [buzzer.cpp, main.cpp]
2019-07-01 kind of fix ir?
    [buzzer.cpp, hardware.h, main.cpp]
2019-07-02 fix dribbler from thomas
    [com.cpp]
2019-07-02 Adapt the robot to the competion (turn correctly)
    [drivers.cpp, ssl.h]
2019-07-03 wip fix dribbler stall
    [motor_hall.cpp]
2019-07-03 Remove a bug in Hall vectorial command
    [motor_hall.cpp]
2019-07-03 HALL is OK and tare only once (FOC)
2019-07-03 Suppression de fichiers en trop
2019-07-04 Prepare merge with fix dribbler and ir thresh
    [com.cpp, hardware.h, main.cpp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]
2019-07-05 barbu mode activated on dribbler and CHARGING
2019-07-05 fix bad driver init
    [drivers.cpp, main.cpp]
2019-07-07 Remove a bug in encoder init
    [encoder_magnetic.cpp, hardware.h]
2019-07-10 DJ working, removed RICKROLL at beginnig and remove deprecated PID packet
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2019-08-27 Init GPIO_OUTPUT and PWM for motor
2019-08-27 Declare LED pins + add terminal command for led
2019-08-27 Improve time + debug tool for printing time
2019-08-27 Implementation of as5047d encoder
2019-08-27 Add JTag pin in CUBEMX
2019-08-27 Improve debug function to print data
2019-08-27 Add Encoder + System + errors
    [encoder.h, main.c]
2019-08-27 Add Timer 2 and 3 with interruption + spi interra
2019-08-27 Synchronisation of TIMER 1, 2, 3 with the timer 4.
2019-08-27 Compute angle proccess by using interruptions.
2019-08-27 Correct a priority problem + Improve assert system
    [main.c]
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2019-08-27 Filter angle + remove some system/error bugs
    [encoder.h, main.c]
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2019-08-29 SPI : Add DMA / correct clk config / remove bugs
    [brushless.ioc, main.c]
2019-08-29 Make some optim + Fast mode for encoder + SPI bug
    [main.c]
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2019-09-01 Add motor +simpl. interr. +Reduce PWM update freq.
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2019-09-09 Accurate the filter delay error
2019-09-15 Prepare the use of ADC for reading phase currents
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2019-11-16 Modified way of using the IR. Now based on a counter, no more on timer. Tested and working
2019-11-16 dribble value when on wasn't correct (old driver)
    [com.cpp, main.cpp]
2020-03-12 Saving exampel log
    [example.csv]

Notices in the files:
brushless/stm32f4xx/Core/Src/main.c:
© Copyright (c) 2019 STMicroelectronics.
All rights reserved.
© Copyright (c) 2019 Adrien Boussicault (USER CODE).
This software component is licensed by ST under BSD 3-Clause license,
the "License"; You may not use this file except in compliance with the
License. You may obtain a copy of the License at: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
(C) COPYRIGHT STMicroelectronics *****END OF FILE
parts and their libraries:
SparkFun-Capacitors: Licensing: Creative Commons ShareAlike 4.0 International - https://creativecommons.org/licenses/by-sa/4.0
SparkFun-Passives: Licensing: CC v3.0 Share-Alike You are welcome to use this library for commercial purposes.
